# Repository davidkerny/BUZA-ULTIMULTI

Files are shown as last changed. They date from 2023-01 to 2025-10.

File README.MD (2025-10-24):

# Ultimulti

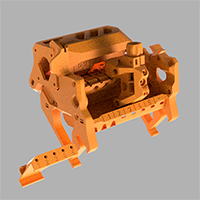
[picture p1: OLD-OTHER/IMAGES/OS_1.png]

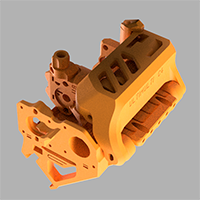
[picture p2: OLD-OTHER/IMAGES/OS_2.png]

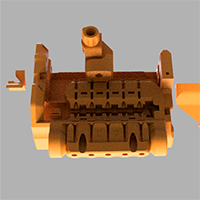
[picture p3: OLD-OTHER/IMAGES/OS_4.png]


**Ultimulti** MMU3 is a DIY multi-material solution developped in parallel with the Original Prusa MMU3, with the ease of use and reliability being the two key improvement objectives, while still maintaining a reasonable reverse-compatibility with the earlier MMU2S. Ultimulti provides more visibility and access to the filament path and the hardware components. This comes in handy in the moment you need to clear out a filament jam or resolve a similar problem at runtime.

- **Prusa MMU2S to MMU3 Ultimulti upgrade**: with just an addition of a few hardware components and printing new plastic parts, you can build the Ultimulti. 
- For **Ultimulti MMU3 build** from scratch; use the Prusa MMU3 hardware components and just print the new plastic parts to get Ultimulti.
  
The most notable advantage of this system is the idler lock which enables you to open and close the idler-body with just a one-handed flick. No longer you have to undo two bolts to reach the MMU's internals - and then re-set the idler tension on both sides. Single idler tension spring inside the lock also mean an easy and precise tension calibration. It allows the MMU unit to home idler axis more reliably due to the single spring having a longer effective deflection range too.
  
Ultimulti should ideally be used as a **full set of plastic parts** of the most up-to-date revision. In case you opt to use just a part of the Ultimulti plastics on your MMU, please refer to the reverse-compatibility milestones and part descriptions below.  
  
When **printing the plastic parts**, the 0.15mm layer height is advised. PETG material is tested to work reliably. As with the MMU2S, the plastic parts are very sensitive to print defects; especially the first layer adhesion and part warping /lifting up from the heatbed. Verify the filament used is dry, the first layer adhesion is sufficient, the part cooling percentage high enough to maintain the dimensional accuracy and the nozzle temperature high enough to ensure a proper layer-to-layer bonding as well as print surface adhesion.

The MK3S+ [Precise Calibration Chimney](
https://www.printables.com/model/209869-mk3s-mmu2s-precise-calibration-chimney) should be used on the MK3S+ extruder. Note, there were several versions of the MK3S+ MMU Extruder Idler parts. Use the latest one.

## Hardware required:  

To upgrade MMU2S to MMU3 Ultimulti, getting a Prusa MMU3 upgrade kit is higly advised as it will get you all the necessary new components.
Apart from the MMU2S parts, you will need:

- MMU2S data cable can be modified to provide a more refined 5V voltage level to the electronics board's logic. A stable 5V supply is crucial! Ideally, the MMU3 cable and PD-board addon should be used.
- 2.5mm ID PTFE tubes should be used. (as on MMU3) 5x650mm, 5x19mm, 1x360mm
- 19mm and 360mm PTFE tubes can be clear color for better filament visibility, however the rest should be regular non-clear PTFE tubes (for reduced friction)
- the rear of the unit is designed to be equipped with 5 E3D collets to retain the PTFE tubes in. (as on MMU3). Alternatively, you can use 5x M6 or M10 pneumatic fittings.
- the selector uses the MK3S fs-lever style 10x6x2 magnet and a 7mm magnetic steel ball (as on MMU3). Note, the MK3S and MMU2S balls are not magnetic!!!
- the idler is meant to be attached to the motor shaft using either a flat-faced metal coupler (MMU3) or a printed adapter with a modified GT2-16 pulley. Remember, - idler concentricity is crucial! Original Prusa coupler is of better quality than the chinese ones.
- M3 washer for the Chimney calibration screw. (MMU3)
- then just sum bolts n nuts. The majority can be harvested from MMU2S. Extra M3nS square nuts are required.
- optionally, 8x6 or 8x5mm magnets for motor visualizers

The magnet, washer, blades and fasteners can be sourced from MK3S and MMU2S spare parts.

## Important development milestones for reverse-compatibility

  ### Idler body/ pulley body OS(one-sided) C-series 

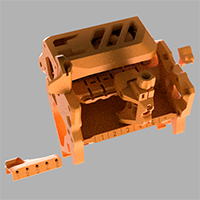
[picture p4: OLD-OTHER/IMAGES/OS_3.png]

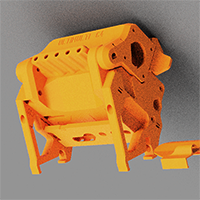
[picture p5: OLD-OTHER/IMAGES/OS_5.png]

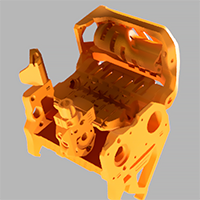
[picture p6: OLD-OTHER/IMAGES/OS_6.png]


- Single lock; on the left side only. Even more filament path visibility. 
- Still compatible with, but shouldn't be used anymore with the fully-printed MMU2S idler due to a commonly occuring idler runout / wobble causing filament loading and idler homing issues. Idler with metal 5mm shaft coupler or GT2-16 pulley should be used instead.
- Allen key storage is now on the left side of the Pulley body (2.5mm, 2mm and 1.5mm long ones) 
- To be used **only** with the bottom-mounted electronics and the corresponding legs that retain the control board below the pulley body.

- Front PTFE holder since B15: grooves between the filaments for easier waste management after cutting function was initiated.
- Selector B19 EXPERIMENTAL has a larger internal filament entry after FINDA, similarly to the pre-B14 selectors. This should aid loading curled filaments. Might have impact on Spooljoin and operation with stringy filaments. Must be tested thoroughly.
- Selector since B17: openings to superglue the bronze bushings in, in case these do not hold in properly. (Usually, they don't only if the parts were printed incorrectly.)
- Selector since B14: different filament entry after FINDA and large opening for clearing out strings from under the FINDA ball.
- Selector since B14 no longer compatible with blade holder <B16 as well as the MMU3 blade-holder. Selector since B14 necessitates the use of blade holder B17 or newer.

- Idler body since C5_3 and C6: Idler tilted down on the right side to equalize the idler tension across all the filament positions. (backlash and idler-body flex compensation) Version C6 is tilted by 0.3mm. Version C7 is tilted by 0.5. Experimental versions of the C7 idler tilted by 0.8 and 1.4mm. Might require further testing.

  ###  Idler body /pulley body Bxx; labeled as Classic - doublelock version.

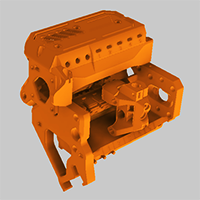
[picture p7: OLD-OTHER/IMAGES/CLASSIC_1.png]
CLASSIC

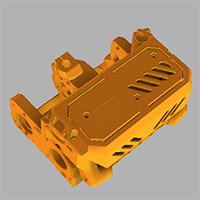
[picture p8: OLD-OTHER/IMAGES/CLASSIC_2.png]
CLASSIC

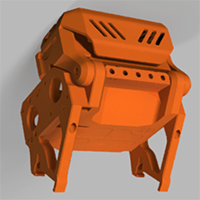
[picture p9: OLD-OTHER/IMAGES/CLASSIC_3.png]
CLASSIC


- The last version to be used with locks on both sides; but found to work even with just the left one in place.
- Compatible with all electronics mounting options: open-back or closed-back cover on top (as in the picture above) or the bottom mounted. (C version)
- Idler body since B20 Compatible with PD-board addon (MMU3) that should be held in by the Addon retainr part. 
- Idler body since B20 incompatible with MMU2S. MMU3 compatible. There is a hex-key storage on the right side of the Idler body.  

  ### Idler body version <B19 (obsolete)

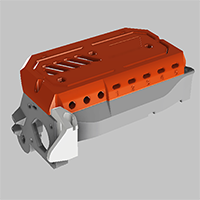
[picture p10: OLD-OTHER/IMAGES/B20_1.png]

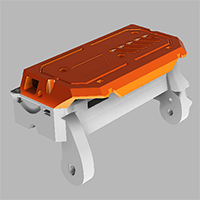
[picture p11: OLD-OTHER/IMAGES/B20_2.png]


- The last idler body compatible with MMU2S pulley body M1/R1. If you are too lazy to replace Pulley body on your MMU2S; using this version, you can upgrade your MMU2S to idler locks.
- printed locks on both sides instead of the M3x30 idler tension bolts directly attached to idler body. Some older versions of the locks have more clearance to account for fully-printed idler's wobble.
- Incompatible with MMU3 PD-board Addon and cable. Old MMU2S data & power cables should be used. There is a zip-tie attachment point for the cables.
- a notch below the connectors for easier MMU2S power/data cable removal using a hex key. Insert the hex key from side to undo the safety latches on the connectors, while pulling the connectors out.
- to be used mainly with the open-back electronics cover (up to B14) - as seen in the picture above - for easier cable management.
- in case it is used with the old fully-printed idler, might require different locks as the printed idlers usually need to compensate the idler eccentricity with idler tension setting. Different older versions of the locks vary in dimensions.

- Ele cover TOP_NOLOCK_B8 version with idler tension bolt retainers is compatible only with the MMU2S Idler body M1/R1 without the Idler locks. Electronic board torsion strain relief cutouts and TMC venting openings. Zip-tie attachment points for easier cable management.

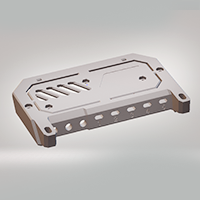
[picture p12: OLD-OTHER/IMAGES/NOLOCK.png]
NOLOCK


- IDLER_BODY_A1_MMU2S should allow the MMU3 PD-board addon to be used on the stock MMU2S. (experimental)

  ### Experimental

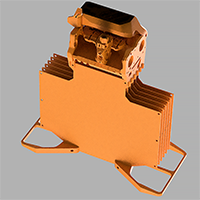
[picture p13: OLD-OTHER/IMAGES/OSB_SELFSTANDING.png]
OSB


- **OSB** version / D-series: freely standing C-series UltiMulti MMU integrated onto the MMU3 Cassette buffer.

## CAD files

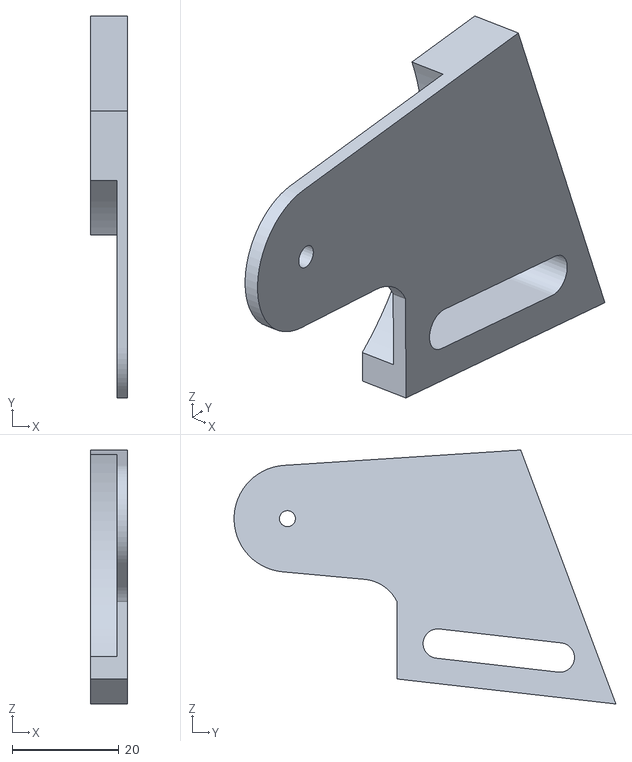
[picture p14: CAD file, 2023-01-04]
AUTOBUFFER/1/OUTPUT.stl
7.00 x 71.5 x 47.6

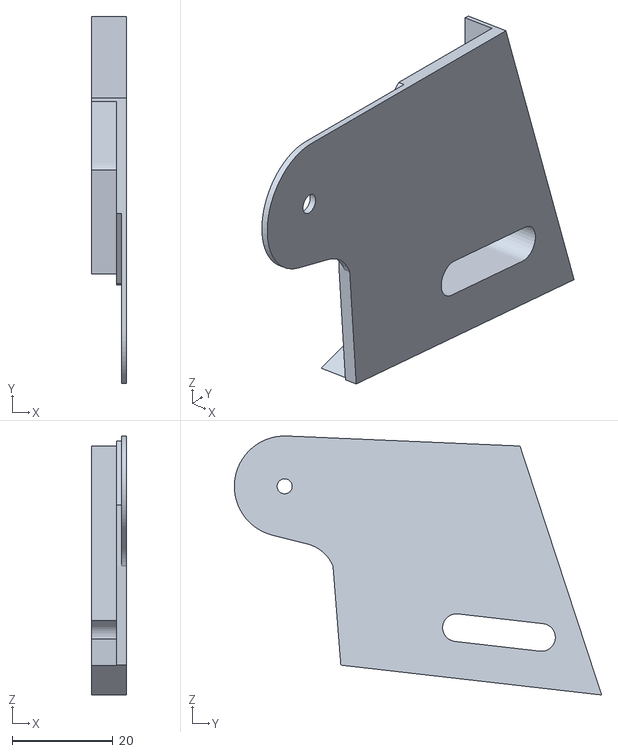
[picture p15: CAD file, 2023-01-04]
AUTOBUFFER/3/OUTPUT.stl
7.00 x 72.9 x 51.4

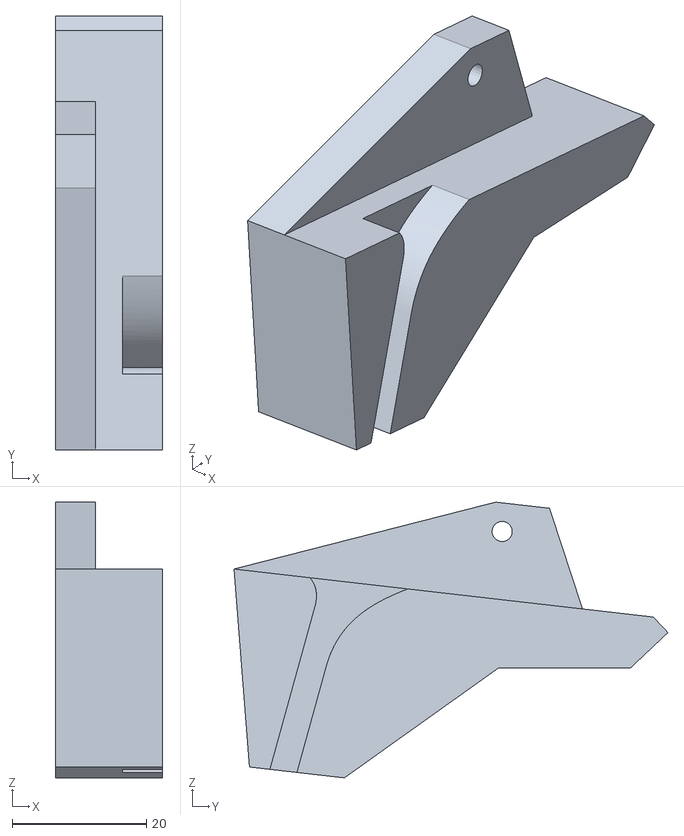
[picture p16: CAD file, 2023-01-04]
AUTOBUFFER/SLIDER OUT.stl
16.0 x 64.6 x 41.1

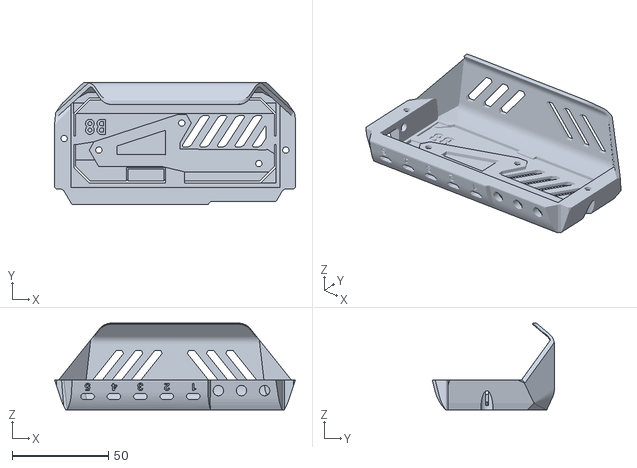
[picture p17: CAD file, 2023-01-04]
CLASSIC DOUBLELOCK VERSION/CLASSIC_ELECOVER_TOP_CLOSEDBACK_B8.stl
125.0 x 63.2 x 45.0

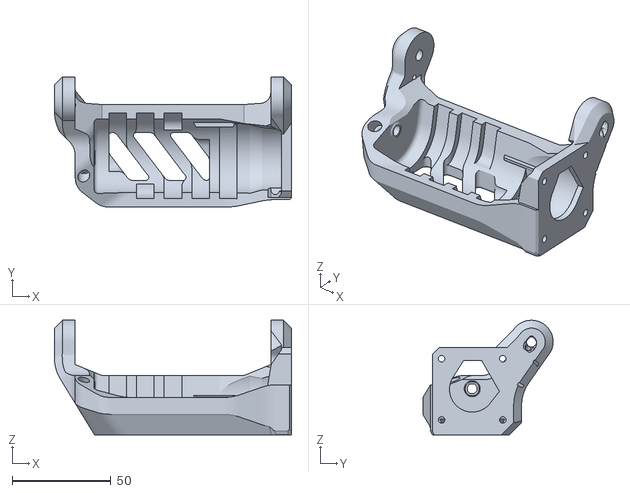
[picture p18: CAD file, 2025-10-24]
IDLER_BODY_C7_M05.stl
120.0 x 66.0 x 58.0

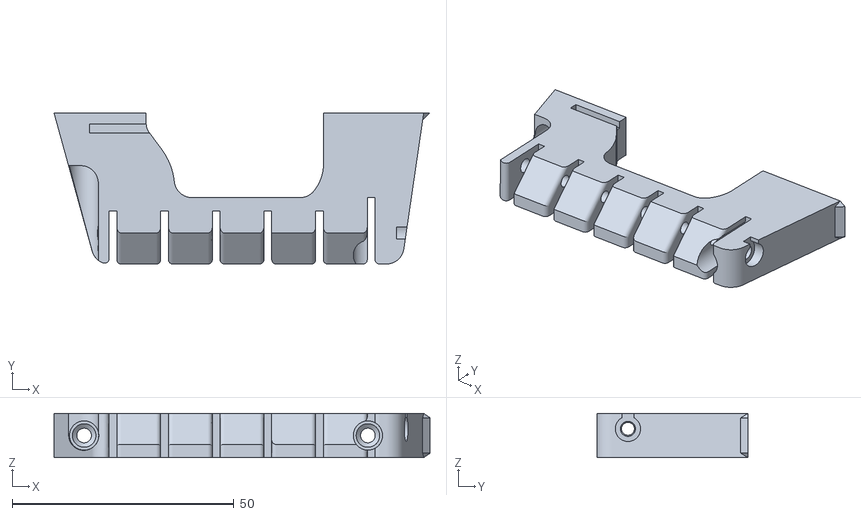
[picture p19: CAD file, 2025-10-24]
OSB SELF STANDING/LEG OSB D3 L.stl
84.8 x 34.1 x 10.0

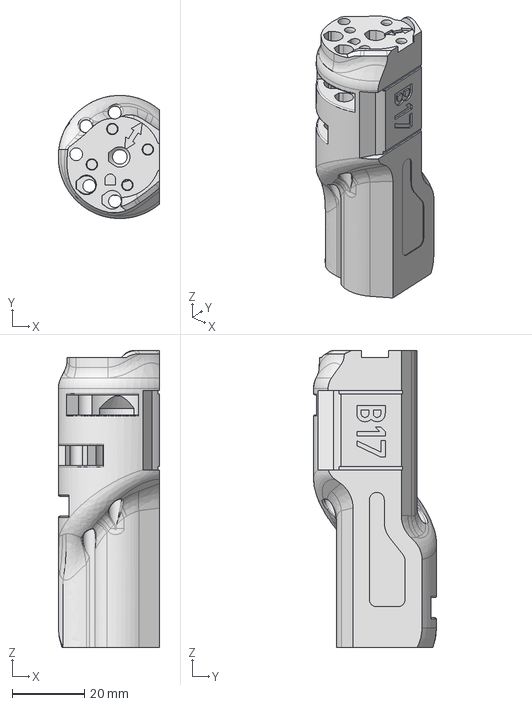
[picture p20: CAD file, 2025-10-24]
STEP/Idler barrel v18.step
28.0 x 34.0 x 82.0 mm

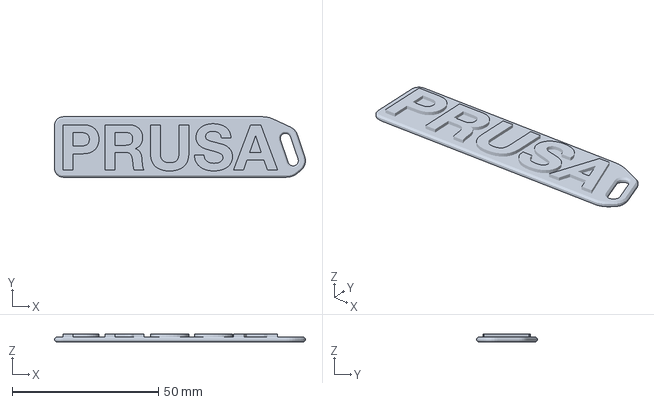
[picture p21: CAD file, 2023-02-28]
TEST OBJECTS/PRUSA_KEYCHAIN.3mf
85.8 x 20.7 x 2.70 mm

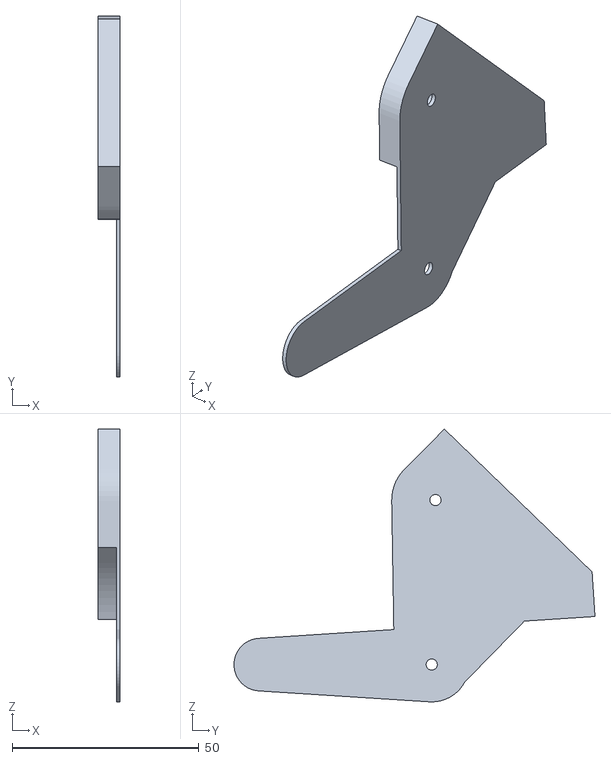
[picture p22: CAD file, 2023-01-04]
AUTOBUFFER/1/INPOUT.stl
6.00 x 96.6 x 73.0

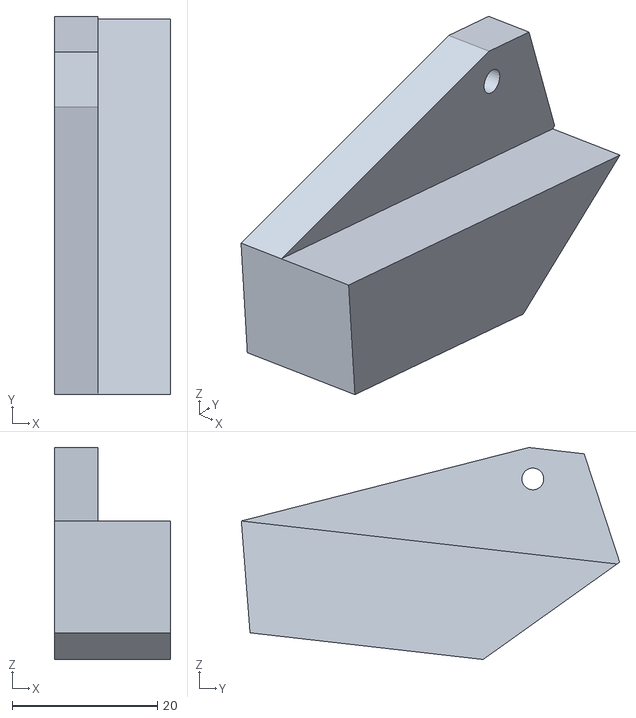
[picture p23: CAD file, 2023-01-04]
AUTOBUFFER/3/SLIDER OUT.stl
16.0 x 52.0 x 29.1

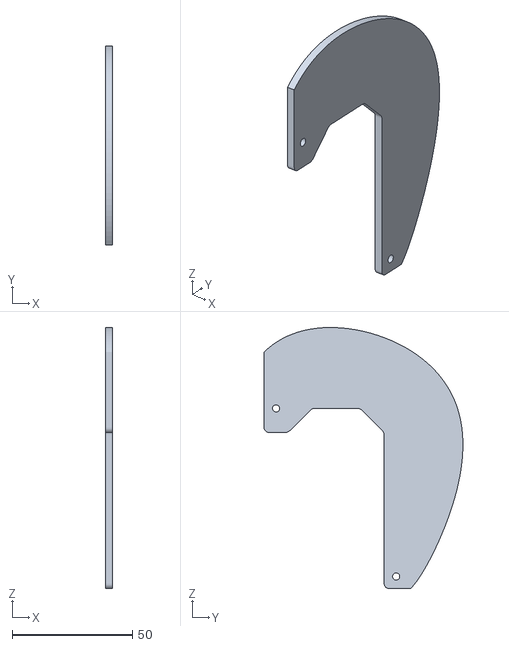
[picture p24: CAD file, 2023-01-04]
AUTOBUFFER/PLATE TEMPLATE.stl
3.00 x 82.8 x 108.7

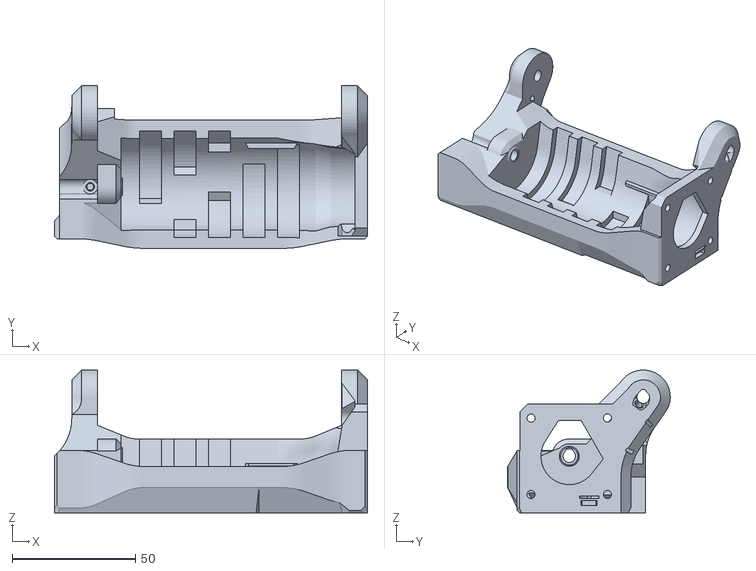
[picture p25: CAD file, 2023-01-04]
CLASSIC DOUBLELOCK VERSION/CLASSIC_IDLER_BODY_B35.stl
127.0 x 66.0 x 58.0

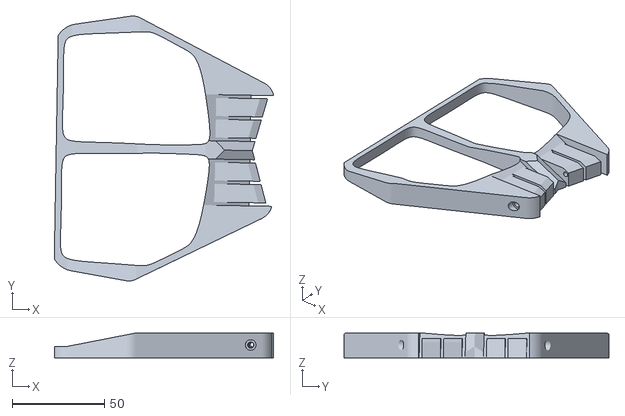
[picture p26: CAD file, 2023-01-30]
OSB SELF STANDING/BUFFRSTAND_ANGLEDSIDE_OSB_D2.stl
119.0 x 143.7 x 13.5

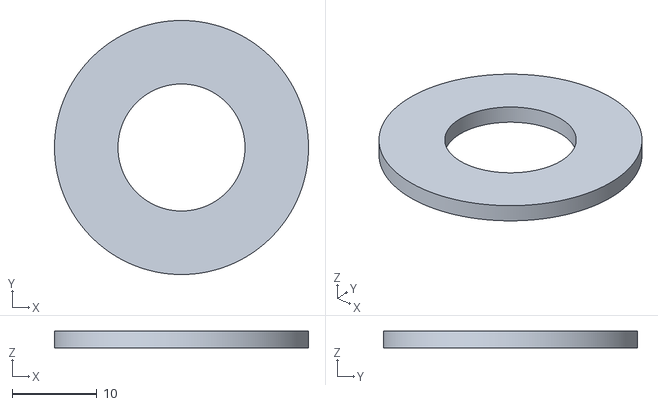
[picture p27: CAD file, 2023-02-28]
TEST OBJECTS/MMU_5COLOR_TEST.stl
30.0 x 30.0 x 2.00

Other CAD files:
IDLER_BODY_C7_M08_Experimental.stl
AUTOBUFFER/1/SLIDER OUT.stl
AUTOBUFFER/3/INPOUT.stl
AUTOBUFFER/s-buffer-plate.dxf
A-Precise-Chimney-Base_7.stl
A-Precise-Chimney-cover.stl
A-Precise-Chimney_6.stl
A-easy-fs-cover-mmu2S.stl
AUTOBUFFER/INPUT.stl
AUTOBUFFER/OUTPUT.stl
AUTOBUFFER/WHEELL 70.stl
CLASSIC DOUBLELOCK VERSION/ADDON RETAINR.stl
CLASSIC DOUBLELOCK VERSION/CLASSIC_LEG_B2.stl
CLASSIC DOUBLELOCK VERSION/CLASSIC_PULLY BODY_B10.stl
COLLET HOLDR C7 M10.stl
COLLET HOLDR C7 M6.stl
COLLET HOLDR C7.stl
COLLET HOLDR_B4.stl
ELECOVER_BOTTOM_C13.stl
ELECOVER_BOTTOM_C5.stl
FILAMENT SAMPLER_3.stl
FINDA ADJUSTR_B2.stl
FINDA CABLE RETAINR.stl
FRONT PTFE HOLDER B10.stl
FRONT PTFE HOLDER B11.stl
FRONT PTFE HOLDER B11a.stl
FRONT PTFE HOLDER B15_EXPERIMENTAL.stl
IDLER COUPLER GT2-16T_V7.stl
IDLER_B14.stl
IDLER_BODY OS C4.stl
IDLER_BODY OS C5.stl
IDLER_BODY OS C5_3_CIRCLES_05COMP.stl
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

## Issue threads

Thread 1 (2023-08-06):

M5 Festo fittings ?

bryn51, 2023-08-06:
Is it possible to have a version of 5 x PTFE tubing holder that takes M5 threaded brass inserts (for Festo QSM-M5-4 Pneumatic).  These I already have, whereas I would have to order in the M6 or M10 sized fittings.
For the collet style, I'm looking at the E3D style "Embedded Bowden Collet for Metal (1.75mm)" - is that the right one ? Also has a clip "Collet Clips (Pack of 2) - 1.75mm × 4" seems useful for locking the collet in place.

Really, a proper BOM would be handy, giving official part numbers that can be searched for, ensuring money isn't wasted on buying the wrong things.

bryn51, 2023-08-07:
Thanks David for your reply.

I’m currently printing your parts-set for upgrade if an MMU2S connected to
a Mk3S+ printer. to gain advantage of the many improvements. With a mind to
a full upgrade when Prusa release the MMU2>mmu3 upgrade kit. But that will
not be until late August.

I’m particularly interested in your specific upgrade of the idler cover
because this is something I recommended to prusa in September of 2022, in
report I wrote and shared with them.

The means of securing the feed-in filaments is also of  interest to me
because of the  many times I’ve had to clear those darned tubes and had to
pull apart the mmu2  to do so.

In regards your project, from my perspective it would be much easier to
build if there was a BOM listing specific products and sources like those
collets or 6/10 mm festo fittings with mating bushings, since I do not
actually have prusa’s  kit, and cannot currently order it.

Many thanks
Bryn Parrott

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
--
Bryn Parrott
Taichung, Taiwan
Ph +886 912448228

davidkerny, 2023-08-11:
Hi!

I've seen you mentioning your 2022 report before - but wasn't able to find any specific information about that. Sounds interesting though. Can you maybe share the exact report you sent to Prusa back then? What channel you used to contact Prusa?

I will try to make an assembly video / guide and BOM once I find some time to do it ;)

D.

bryn51, 2023-08-11:
Hi David,

Its an awkward thing.  I told them at the time it was confidential to them as the only recipient.

You have to promise to share it with anyone, nor give reference to it.

Its not a secret report, but I wanted not to embarrass the company by doing what everyone else was doing, and vilifying them.  The language in the report is neutral, not  emotive throughout.

I like to think that it was listened to, as evidence indicates not soon after that, they started work on the MMU3. And implements most of the recommendations in the report, plus a few of their own.

Can you make an undertaking not to share it ?

Thanks,
Bryn Parrott

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

bryn51, 2023-08-13:
Hi David,

As mentioned, I have printed out your kit of parts to build the UltiMulti version of MMU3.

And its basically done, waiting on delivery of various parts over the next 6 weeks from different parts of the world.

However now that’s done, I also printed the buffer unit with revised design by Prusa.

And then tried to fit it into my Prusa Original Enclosure, discovered it does not actually fit as designed by them.

There are various things wrong, but the lain thing is that the part that secures the buffer to the printer frame is wrong size, and also the buffer will not fit alongside the right of the printer, there isn’t enough space alongside the right of the Frame Z axis.  Clearly Prusa forgot that some people might actually have the Enclosure and want to use it with a printer having the MMU3 fitted.

So it occurred to me that this is something you might want to tackle.  It requires only a couple of parts to be designed.
One is the mount.
The other is a small part to feed the tubing from outside the enclosure in toward the buffer.  There are 3 possible holes in the enclosure that might suit people in different situations.
One on top of the lid in the middle, another in the central back of the enclosure lid, and a third on the right corner (vertical) of the rear window of the enclosure. (thay are all different shapes.  But whats needed is a plastic part having 5 x 4mm holes to accept the tubing and hold it secure.

So, for your consideration.

Cheers,
Bryn Parrott

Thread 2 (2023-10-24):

PDU Board added to electronics hangs below the frame - can hit extruder in highest Z position

bryn51, 2023-10-24:
Yesterday, my Upgrade kit froMMU3 arrived, and the only thing I needed for it, having built UltiMulti weeks ago, was PDU Board.
So I installed it, then went through some routine tests.  Extruder at some stage went to highest Z position, and I discovered if extruder was moved left/right, it strikes the PDU Board. Also some wires dangling beneath the MMU hit the extruder wire harness. Can't be good.  Can't ignore it.
I considered mounting electronics above the board, but this would involve throwing away some of the Ulti Multi benefits  so its a no to that idea.
So, now I am looking at the legs design, both standard and Bear, to see if MMU can be mounted higher by about 5mm. will post a remake on printables if it succeeds.

bryn51, 2023-10-25:
I made a remix on Printables to alter the legs and accommodate the PDU without interference to Extruder movement at highest Z position.  https://www.printables.com/model/626377-mmu3ultimulti-revised-leg-for-pdu

You are welcome to include that alteration in this distribution if you approve of it, and you wish to do that.

davidkerny, 2023-10-26:
Hi!
The idea for the Ultimulti C version (electronics on the bottom) was to bend the PD board addon to the back so that it doesnt take up as much space below the MMU unit.

These is a small notch on the inner side of the right-side leg indicating how much to bend the PD board's connector to make it fit. After bending, the PD-board should snap into the notch. The PD-board in this position might be visible in some of the photos on Printables.
Bending the connector might be creepy. Some users will probably be uncomfortable with doing it and might find your design better. So, thanks for the remix!

bryn51, 2023-10-26:
Hi David, and thanks for responding,.

As background, I have a life experience of 20 years working as electronics technician for a large Telco, and this included board repair to a high standard. (Repair of damage caused by lightning strikes).

But now I’m a “little” older and retired from all that.  So, with that experience and knowledge of consequences should I F&*k it up, and not having spare boards on hand, I am indeed reticent about bending the connector pins in that way.  If the pins should break or become unsoldered then it will be unreliable, and any damage like fine cracks is not always visible.
Since the goal of PDU board is to make the MMU3 more reliable than MMU2, bending the pins seems to work against that theme.

I have made the replacement legs that were remixed, and the modification seems to work OK.  Time will tell if I made them strong enough.  I used the strongest material I have on hand, but only 2 perimeters and 15% infill.

My suggestion would be to add a section to the printables and github readme about that modification, as it is not obvious, but I had noted the little slot on the original left side leg and wondered about its purpose.  It just did not occur to me to bend the pins. (Duh – right !).
Inclusion of the two photographs would be a bonus.

Anyway, I am happy for you to make the altered leg design available since it has now been tested and seems to work.

Thanks for a great design on the UltiMulti, it must have taken a LOT of effort, which is commendable.

I have the MMU3 for Mk4 printer on order.  As a full kit it comes with everything already printed. Easy to just go with it.  But the utility of the UltiMulti is just so much better, I am wondering now if I should prepare for “someday soon” release of the MK4 version of MMU by printing the UltiMulti plastics over again.

Anyway, Tks again and Cheers,
Bryn Parrott

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

Closed 2023-10-25.

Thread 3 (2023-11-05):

Error 04125 at first MMu homing

FelixGraf404, 2023-11-05:
Hey,

I have the problem that the MMU3 (Ultimulti) with the firmware >= 3.0.0 do an strange rattle noise and can´t reach the homing Position for the Idler.

Change the sensitivity (4-7) in the threshold menu do nothing, same prob again.

The idler can move free, nothing blocked. The "endstop" of the idler part is reached perfect.

Have no idea to solve that problem. At the moment i use firmware 3.12.2/1.0.6 without problems.

davidkerny, 2023-11-05:
Hi Felix.
I have encountered something similar as you describe, after tinkering with the Idler TMC sensitivity and homing speed registers, via G-codes. I probably managed to mess up come contents of the EEPROM and the MMU unit was no longer able to even start homing the axis.
What helped was to perform a factory reset:
https://help.prusa3d.com/article/factory-reset-mmu_510075

Could you try the factory reset to see if it helps?

The FW 3.0.2 is miles better than 1.0.6 and the idler sensitivity Tune menu should be able to sort out any of the problematic Idlers.  Some other possible causes might be the hardware ones: idler coupler not being tight or aligned properly, idler tension too high etc.

FelixGraf404, 2023-11-07:
Hey David,

Thanks for your fast response,

I put the 3.13.2/3.0.1 combo on my Printer and dis the reset Like in the PrusaHelp Page.

But the Problem come back. The idler Rattle Like before (sensitivity 4-7) did nothing.

davidkerny, 2023-11-09:
@FelixGraf404
Hi! In the cases I have seen so far, similar issues were caused mostly by hardware faults such as
1. wobbly Idler without the metal coupler that didnt rotate properly,
2. idler being pushed to the side so much, that it was hard to move it,
3. foreign object causing the idler not to rotate properly or similar.

There has been edge-cases reported of Idler stalling when rolling over the filaments - which might lead to MMU selecting a different color by accident. But if your idler doesn't home with any of the sensitivity settings (sg_threshold 4-7), it is weird. So far, it seems that one of these settings should work on any machine.  Can you maybe make a detailed video of the MMU while malfunctioning? In case we find out what's wrong and what helps in this case, I can share the findings with the developers to evaluate them.

The idler currents are set to produce the correct amount of force with the exact type of the motor as there is on the Idler / Pulley / printer's Extruder. If you use a different type of motor, it might not work correctly.
 In case there is a problem with the electronics, such as a TMC malfunction, the firmware 3.0.0 and up should notify you about something being wrong. (TMC not responding, reset, overheat, communication error, undervoltage error etc.). If there was no such error screen, I would assume there might be a hardware error.
 In case you have used an original prusa MMU3 upgrade kit, you might also try to reach out to prusa support to see if they can provide an insight.

FelixGraf404, 2023-11-09:
https://github.com/davidkerny/BUZA-ULTIMULTI/assets/105812017/74bba0c9-a2fb-4557-a465-4824fcc4c0e0

The idler rotates Sweet Like Butter. (Vid1)

My Setup:

Fystec Mk3s clone
The Mmu was an fystec mmu2s, the Upgrade Kit is an original Prusa Kit
(The present Poor Student wanna Print, so he has to but fystec stuff 🤪)

The error:

https://github.com/davidkerny/BUZA-ULTIMULTI/assets/105812017/e68e1e90-2c43-40e6-8018-f59c4e8ee1af

https://github.com/davidkerny/BUZA-ULTIMULTI/assets/105812017/528459b4-9c8b-4f2c-a9fd-192a58bb0043

davidkerny, 2023-11-14:
Hi! Your Idler motor seems to be a bit larger than usual. It is possible the homing just requires some more tuning to fit your hardware. When looking around the available options, the TZB firmware seems to home the Idler more reliably using sg_threshold 7 - which is default even for MMU3. It is using a faster homing feedrate though. I would suggest trying a faster homing feedrate. Otherwise, I'm out of ideas :(

It should be possible to change the feedrate using the M708 command:
https://help.prusa3d.com/article/registers-mmu-mmu3_511780
If it doesn't work, you can also try to reach out to the Prusa Github for help.

D.

FelixGraf404, 2023-11-21:
News from my MMU:

I ordered an original Prusa Idler Motor, installed him an the mmu homes With no Problems. So the "tuning" of the Motor Parameter should be the key of the Not Home Problem (#04125)

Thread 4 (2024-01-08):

FRONT PTFE HOLDER B15_EXPERIMENTAL.stl

slaesh, 2024-01-08:
just a note, dont know if it is on purpose or not..
the B15 experimental part uses M3x18 screws, instead of M3x10 like the rest of the parts :)

davidkerny, 2024-01-08:
Hi!
Do you mean the COLLET HOLDR C7 (the rear PTFE holder)?
M3x10 might be a bit too short in this place.
Two M3x18 bolts are used to hold the electronics on top of MMU2S / MMU3 - you can reuse those :)

(the Rear PTFE holder on MM3S as well as collet holder on MMU3 both use M3x10 bolts in this place - but these parts are mounted slightly differently.)
David

slaesh, 2024-01-08:
Hey David, thanks for that info do! :)

Oh, yeah. sh*t! it's the C7 🙈🙈 You know your parts though! ;)

I have enough screws .. was just wondering and wanted to ask you.. since I thought it was the experimental part 😅 :))

Awesome work btw! Have a great 2024

Closed 2024-01-08.

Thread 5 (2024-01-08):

SELECTOR_B18.stl

slaesh, 2024-01-08:
this part maybe could need some more strength at the clamping part:

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

it broke, i did not forced it too much.. its just plastic! ;)
but the SuperFINDA was still loose.. after tightening it up enough.. like 5-10 seconds later.. I heard a "click" :(

davidkerny, 2024-01-08:
Hi!
Thanks for the report.
This has been happening once in a while on the MMU3 selectors too. I've been searching for a solution but then found the craked finda holders still serve the function so I left it as it was.
Maybe the FINDA-holding part should be thinner, less constrained, more flexible. Let me know if you have ideas to make it work with different materials and print settings :)

D.

slaesh, 2024-01-08:
Yeah I will let it sit for now too :)) seems to do it's job 🦾
Hopefully being able to do some test prints on the weekend 🤝😎

Closed 2024-01-08.

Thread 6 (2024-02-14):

Would you share step file?

chloePrinter-box, 2024-02-14:
Hello,
I am part of a company that creates enclosure for Prusa printers. I have a user that would like to use its UltiMulti MMU3 system with our enclosure, but I can't tell if that would work, as we don't have the outside dimensions.

Would you share the STEP file of the assembly?

That is not for a commercial profit, as we will not sell it. We may only advertise that our enclosures works with your system.
You can contact me on chloe@printer-box.com

Thanks!

jltx1, 2024-05-23:
I would also like STEP files for non-commercial use.  I would share any improvements for consideration.

The latest PD board add on from Prusa has been rotated 90° and is no longer compatible with your mount.  I need to add clearance for the pcb and possibly raise a few mm to clear extruder when at the top.  I have other mods I would like to try as well.

Great design overall.  I was going to do this same project a few years back on mmu2 but didn’t get time.  I’m glad you did.

jltx1, 2025-01-20:
I've made several changes but now reached the limit of what I can hack on imported STL files.   And some of the parts don't import correctly.  Any solid model would be much appreciated.

Please consider releasing the current version as STEP so others can leverage your great design.

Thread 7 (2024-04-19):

MMU3 R4 compatibility

HonzaJaros, 2024-04-19:
Hello,

could you confirm that ultimulti is fully compatible with new revision on printables. the R4?

With the official release and Shipping of mmu4 for MK4, is it going to be needed an update to R4 Standard of ultimulti for mk4?

As Průša mentioned, There was some extensive testing and changing some parts recently…. they just published R4 STLs

My kit will come soon, so I am thinking to print ultimulti and skip the printing the Prusa mmu3 printable parts if better than R4.

thanks for your feedback or update :)

davidkerny, 2024-04-20:
Hi!
The prusa mmu3 R4 update adresses these issues:
- Parts were optimized for the updated prusa print farm with MK4 IS printers instead of MK3S. Mainly tolerances of small openings have changed. This is not a concern for the home-printed parts. However, this is the reason all the part markings have changed.
- Selector blades have been re-positioned. Insufficiently clamped selector blades have been adressed in Ultimulti selector in the past already.
- Selector has openings for easier insertion of the bronze bushings. This hasnt been an issue in ultimulti + there are small holes for gluing the tubes in.
- Rightmost Idler shaft kept falling out. Already fixed in Ultimulti a long time ago.
- Taller electronics cover and the pd-addon board cover: These are just an ESD compliancy additions that are recommended, not mandatory. Interestingly enough, for the MK3.5 (which is also xBuddy driven ), it is not required to change even as a recommendation.
- The only mandatory R4 printed part for MMU3 are the newer buffer cassettes. (along the extruder printed parts included in the kit)

Since, Some of the features from Ultimulti have been used in MMU3 and vice-versa, both will do the job.
I've been using both versions with the same level of reliability on the MK4.
Personally, I of course prefer the Ultimulti due to the control over what's happening inside and due to being biased, but ultimately, the decision is up to you ;)

HonzaJaros, 2024-04-20:
Thank you david for comprehensive answer!

as a soon to be new owner of mmu3 could you please point out  in wiki  what part must be printed from Prusa as compulsory for ultimulti. I am little bit lost in those name files…

thank you

Closed 2024-04-20.

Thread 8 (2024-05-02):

Selector B18 - Filament hitting a wall

corporategoth, 2024-05-02:
I've printed these parts with a Prusa MK4, in Prusament PET-G, 0.15mm Structural.

If you have a filament that likes to 'curl' or as a natural curve, then often it will 'follow' the ball baring in the selector.
The hole for the filament to exit the selector is too small, or at least, the guide for filament to follow the path is not big enough.
When this happens, the filament hits the wall inside the selector, and cannot exit the selector.

The selector should be designed to either better constrain the filament so that it can't curve (difficult since that will hinder the ability to move the ball baring), or the channel to guide filament into the exit hole needs to be bigger to allow for filament that likes to curl/curve upwards.

I had this problem happen repeatedly with my Polymaker PET-G filament.

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

davidkerny, 2024-05-07:
Hi!

The filament curling, as you describe, usually happens only on the first load of a new filament.
I wasnt able to reproduce it with a filament that has a tip formed in the hotend. That would mean, that straightening the filament end (as the MMU3 handbook and assembly guide suggest doing before preloading a filament), would fix it.

The selector B11 (to be used in combination with blade holder B14) had a larger filament entry after FINDA ball, as there is on the original MMU3 selector.
This larger entry point used causing three things:
1. curled filament was able to load more easily.   2. Unloading a depleted filament with a curl at the end was often unsuccessful. (spooljoin) 3. strings were entering the filament entry often jamming the filament transport path.
The smaller entry point has fixed all these issues. Not only that, Now, I was able to print very stringy materials unlike before, as the filament strings were diverted sideways, and exited the finda ball chamber more easily after fine-tuning the geometry.

Due to the larger side openings around the FINDA ball, the conical entry cannot occupy the same space as it used to on the selector B11.  I tried reconstructing the shape to fit the most up-to-date selector. The result are some geometrical weirdnesses but it should work similarly to the B11 version. Please, test it to see if it helped with the curled filament:

https://github.com/davidkerny/BUZA-ULTIMULTI/blob/main/OLD-OTHER/SELECTOR_B19_EXPERIMENTAL.stl

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

corporategoth, 2024-05-08:
Here is what I managed to create using PrusaSlicer to add negative volume modifiers

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

corporategoth, 2024-05-15:
@davidkerny FYI - your B19 seems to be doing the trick, I am not hitting the wall anymore on my MMU3 print.

I didn't even have to use my modification to it (with the longer top) - your printed part was sufficient.

corporategoth, 2024-05-15:
One other thing I will mention is that I think the holes for the brass tubes are slightly too big.  They don't "hold" onto the brass tubes well enough so the brass tubes will slip out of the selector, and end up in a random position on the rods they are sliding over, as opposed to sticking to the selector.

firetech, 2024-06-20:
Just to add my 2 cents to the discussion:

I've been running the UltiMulti as intended (i.e. with Selector B18) for some time, without any issues, mainly printing PETG. When I loaded some PLA that was nearing the end of its roll yesterday, I experienced this issue. It was happening repeatedly, basically every time the filament was loaded again. Switching to the B19 selector seems to have solved it, even if I intentionally make the filament even more curved.

Furthermore, I don't have any issues with the brass bushings sliding out, I'm not even sure I can get the ones in my B18 selector out without damaging anything (luckily, I had extras)...

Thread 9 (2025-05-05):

LEG OSB D2 L.stl missing PCB cutout.

JarTheHead, 2025-05-05:
The left leg for the self standing version is missing a PCB cutout for the MMU control board, so there isn't enough room to fit the board.

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

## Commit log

2023-01-11 C7 collet holder mod
    collet holder: filament loading angle 4deg upwards towards the pulley, collet holder 7mm longer than the initial version
    [COLLET HOLDR C7.stl, COLLET HOLDR LONG_2DEG.stl, COLLET HOLDR LONG_2DEG_CUTOUTS.stl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]
2023-01-12 Precise Chimney Base v7
    [A-Precise-Chimney-Base_6.stl, A-Precise-Chimney-Base_7.stl, A-Precise-Chimney-cover.stl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]
2023-01-17 Reset physical button on the LEG R C10
    aesthetic tune-up of the idler body
    [IDLER_BODY OS C4.stl, IDLER_BODY OS C5.stl, LEG ELE R V10.stl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]
2023-01-18 Add Idler body C5 & Leg R B10 into 3MF
    minor renaming
    [FRONT PTFE HOLDER B10.stl, FRONT PTFE HOLDER V10.stl, LEG ELE R C10.stl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]
2023-01-18 LEG R: Refined USB opening and New sampler
    New filament sampler with cable holder. To be tested out.
    [FILAMENT SAMPLER_2.stl, FILAMENT SAMPLER_3.stl, LEG ELE R C10.stl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]
2023-01-27 Self standing MMU integrated onto the buffer
    [LEG ELEBUF L.stl, LEG ELEBUF R.stl]
2023-01-27 Buffer stand
    [BUFFRSTAND.stl]
2023-01-28 OSB: refined buffer plate cutouts
    [BUFFRSTAND OSB.stl, BUFFRSTAND.stl, LEG ELEBUF L.stl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]
2023-01-28 Refined bufferstand
    [BUFFRSTAND OSB.stl]
2023-01-29 OSB bufferstand refinement
    ... for easier printing
    + add plateclip
    [BUFFRSTAND OSB.stl, PLATECLIP OSB.stl]
2023-01-30 OSB D selfstanding version update
    [ADDONBOX_A_D1.stl, ADDONBOX_B_D1.stl, BUFFRSTAND OSB_D2.stl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]
2023-01-31 filename unification
    [ALT LEG R_C2.stl, COLLET_HOLDR_B2.stl, COLLET_HOLDR_B4.stl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]
2023-02-03 Selector huge opening and shape improvement
    Huge opening for cleaning debris from FINDA canal using compressed air and FINDA ball visibility. Arrow pointing to one of the numbers on pulley body defining the selector's position. Optimised blade holder bolt position, optimised shape for better blade visibility and debris clearance in the pulley body.
    [FILAMENT SAMPLER_3.stl, SELECTOR_B14_EXPERIMENTAL.stl, SELECTOR_B15_EXPERIMENTAL.stl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]
2023-02-08 experimental design to idler body
    [IDLER_BODY OS C5_CIRCLES.stl]
2023-02-13 experimental Idler tilt compensation
    [IDLER_BODY OS C5_3_CIRCLES_05COMP.stl, PULLEY_BODY OS C7.stl, SELECTOR_B14_EXPERIMENTAL.stl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]
2023-02-14 Shaft opening refinement
    [IDLER_BODY OS C5_3_CIRCLES_05COMP.stl]
2023-02-14 0.3mm tilt compensation
    [IDLER_BODY OS C6_03COMP.stl]
2023-02-14 hex key holder refinement & easier bolt insertion
2023-02-16 filament path refinement for better spooljoin
    [FRONT PTFE HOLDER B11.stl, FRONT PTFE HOLDER B11a.stl, FRONT PTFE HOLDER B15.stl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]
2023-02-27 motor connector hint labels
    [ELECOVER_BOTTOM_C13.stl, ELECOVER_BOTTOM_C5.stl, SELECTOR_B15a.stl]
2023-02-27 improved finda attachment
    [FRONT PTFE HOLDER B11.stl, FRONT PTFE HOLDER B11a.stl, FRONT PTFE HOLDER B15_EXPERIMENTAL.stl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]
2023-02-28 TEST OBJECTS
    [MMU_2_COLOR_TEST.stl, MMU_3_COLOR_TEST.stl, MMU_5COLOR_TEST.stl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]
2023-02-28 TEST OBJECTS: Keychain
    [PRUSA_KEYCHAIN.3mf]
2023-03-21 selector bushing glue grooves
    + minor renaming
    [MMU3_2COLOR_TEST.stl, MMU_2_COLOR_TEST.stl, SELECTOR_B17.stl]
2023-04-06 filename cleanup
    [CLASSIC_ELECOVER_TOP_CLOSEDBACK_B8.stl, CLASSIC_IDLER_BODY_B35.stl, CLASSIC_LEG_B2.stl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]
2023-04-12 even more M3x10 clearance to finda
    [SELECTOR_FRONT_PLATE_B1.stl, SELECTOR_FRONT_PLATE_B2.stl]
2023-04-12 even more M3x10 clearance to FINDA
    M3x10 bolt too close to FINDA might have influenced the FINDA readings slightly on MMU2S, when FINDA was mis-calibrated right on the edge.
    [SELECTOR_FRONT_PLATE_B2.stl, SELECTOR_FRONT_PLATE_B3.stl, SELECTOR_FRONT_PLATE_ORI_A2.stl]
2023-04-13 minor design improvement
    [SELECTOR_BLADE_HOLDER_B19.stl, SELECTOR_BLADE_HOLDER_B20.stl, SELECTOR_FRONT_PLATE_B3.stl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]
2023-04-18 improved gap above the blades
    [SELECTOR_BLADE_HOLDER_B20.stl, SELECTOR_BLADE_HOLDER_B21.stl]
2023-04-20 larger FINDA side inspection opening
    [SELECTOR_B17.stl, SELECTOR_B18.stl, Selector v17b.stl]
2023-07-30 COLLET HOLDER M6 and M10 versions
    [COLLET HOLDR C7 M10.stl, COLLET HOLDR C7 M6.stl]
2023-07-30 Update COLLET HOLDR C7 M10.stl
    [COLLET HOLDR C7 M10.stl]
2023-08-17 BEAR frame legs
    [LEG ELE L C17BEAR.stl, LEG ELE R C17BEAR.stl]
2024-05-07 Create SELECTOR_B19_EXPERIMENTAL.stl
    Larger filament entry after FINDA to aid loading a curled filament.
    [SELECTOR_B19_EXPERIMENTAL.stl]
2024-05-07 Selector B19 Experimental conical internal filament entry
    [SELECTOR_B19_EXPERIMENTAL.stl]
2025-04-04 CORE One holder
    [LEG CORE QUICK RELEASE C19.stl, LEG ELE L CORE C19.stl, LEG ELE R CORE C19.stl]
2025-10-24 Compensation for Better Filament 5 Loading
    Idler Tilt Compensation:
    Right side of the Idler Body sits 0.5, 0.8 or 1,4mm lower compared to the left side, to mitigate issue with loading filament 5, as some users have been reporting.
    The older version of the Idler Body (C6) utilized a 0.3mm compensation which apparently might not be sufficient for some UltiMulti units.
    This modification should result in higher idler tension for the filaments on the right side.
    Needs further testing.
    [IDLER_BODY_C7_M05_Experimental.stl, IDLER_BODY_C7_M08_Experimental.stl, IDLER_BODY_C7_M14_Experimental.stl]
2025-10-24 Filament 5 Loading Improvement
    Idler tiled downward by 0.5mm towards the right shaft to improve loading the filaments on the units right side.
    [IDLER_BODY OS C6_03COMP.stl, IDLER_BODY_C7_M05.stl]
2025-10-24 Update README.MD
    Idler tilt compensation; Idler body C7
2025-10-24 Root Folder Cleanup
    Filament Sampler attaches to the MK3/MK4 frame and stores filament samples.
    Addon Retainr retains the PD-Board Addon on the main electronics board. It is compatible with the classic doublelock B version only.
    Idler Coupler for the de-lidded GT2-16T Motor Pulley is probably no longer a vital component, since the Prusa metal couplers are widely available.
    [ADDON RETAINR.stl, FILAMENT SAMPLER_3.stl, IDLER COUPLER GT2-16T_V7.stl]
2025-10-24 Leg Electronics cutout fix
    [LEG OSB D2 L.stl, LEG OSB D3 L.stl]
2025-10-24 STEP add
    [Idler barrel v18.step]
